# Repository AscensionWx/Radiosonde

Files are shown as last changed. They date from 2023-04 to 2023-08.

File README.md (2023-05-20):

# Radiosonde
Collection of tools for DIY Weather Balloons and Forecasting

For Kanda Weather (Africa) and AscensionWx (U.S.), and open under MIT license.

|  TTGO LoRa32 v2.1     |     Cybaart Kanda Aeolus   |     KandaWeather Launch 
:-------------------------:|:-------------------------:|:-------------------------:
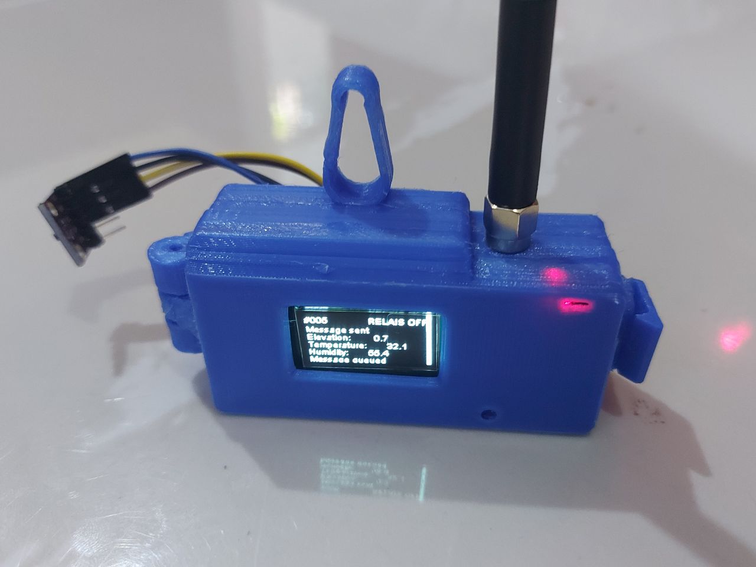
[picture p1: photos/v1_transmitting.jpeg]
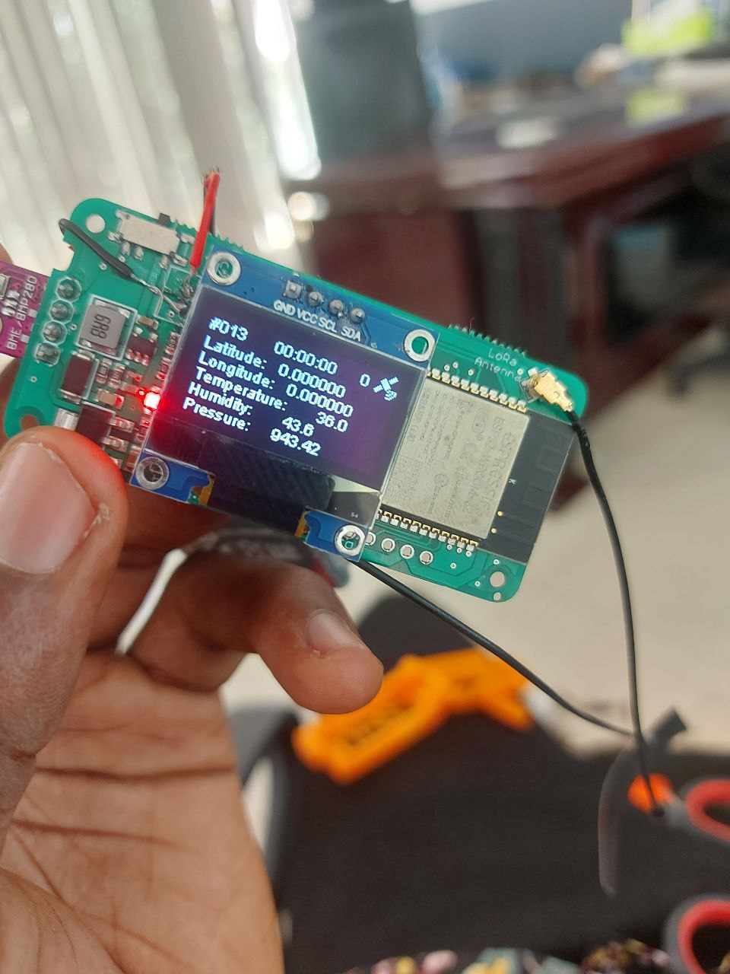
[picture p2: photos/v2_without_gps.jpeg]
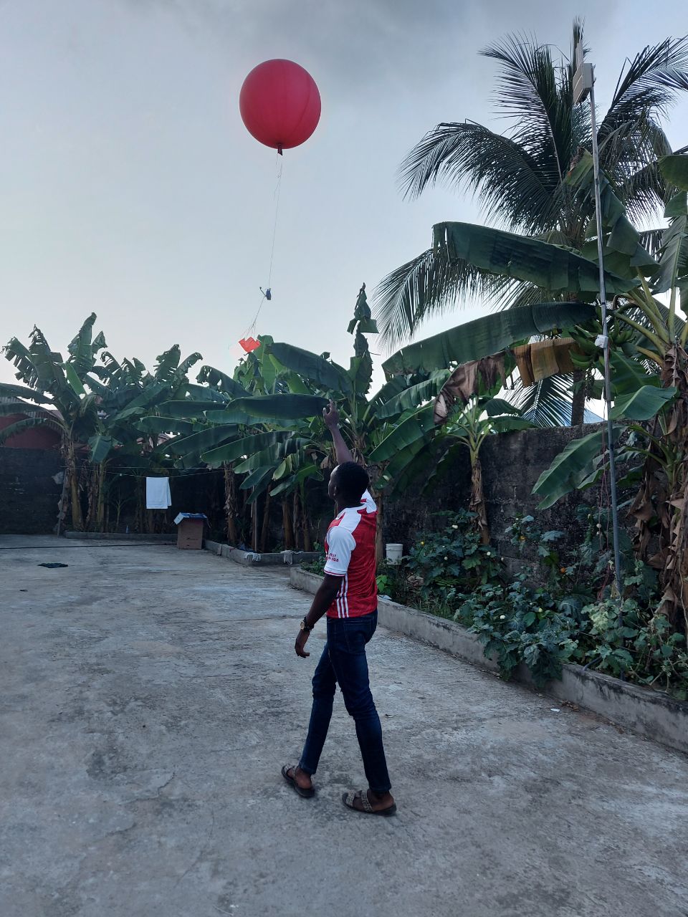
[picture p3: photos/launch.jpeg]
|   |   |   |

Components:
- Hardware
- 3d print files
- Firmware
- LoRaWAN decoders
- Node-red flow files
- Blockchain Smart contract

- Forecasting Dashboard
- Machine Learning Datasets

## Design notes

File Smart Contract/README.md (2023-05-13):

# Smart Contract

The native Antelope C++ smart contract files for AscensionWx Radiosonde Miners.

Features:
- Storage of data from weather balloon launches
- Sends mining rewards in real-time over the course of 90 minutes

Dependencies:
- 1.8.0 eosio CDT

Utilizes other on-chain contracts
- delphioracle
- eosio.evm 

Future additions:
- Device-specific digital signatures

Currently deployed on several contracts such as asensiondal contrct on Telos Mainnet
https://explorer.telos.net/account/ascensiondal

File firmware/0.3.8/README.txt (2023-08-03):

Updates:
Send every 3 seconds for first 150 meters, 5 seconds to 850, 10 seconds to 700, 20 seconds afterwards
checkIfLaunch() function checks if pressure has fallen significantly in 2 consecutive readings
Call checkIfLaunch every 3 seconds while on the ground
Set weather variables as globals
Include -1.0 temperature offset
Apply additional offset based on lux (divide by 9000)
Store 2 minutes of lux
Improve sensor reading handling ... make all global and separate read() functions
Change GPS tx/rx pins to 1 and 3
Submit lat/lon elevation if data ONLY if it's not stale
Light sleep between messages
Set timezone on esp32 and use it when sending observations
We are firmware version 0.3.8, so use ports 81, 82, and 83
Include pressure with status messages that send every 30 seconds
Add unixtime in obs message (since we have GPS and need it for wind)
Add lux avg variable in obs message
Turn wifi off after 2 minutes if no smartphone connected
OLED displays "Turning off screen" for 10 seconds and then turns off
After wifi turn off, sleep between 3-second BME readings and 30-second status msgs
Add time limit check "Time limit reached. Please restart" and sleep

To Do:
Increase power and use SF7 with each transmit e.g. LMIC_setDrTxpow(EU868_DR_SF7, 21)

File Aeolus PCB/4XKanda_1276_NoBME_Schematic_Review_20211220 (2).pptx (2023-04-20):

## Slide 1

4XKanda_1276_NoBME Schematic Review Report

Schematic file: 4XKanda_1276_NoBME.sch
Date: 12/20/2021

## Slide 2

Summary

No. | Description | Status
1 | Incorrect the value of input capacitor (C5, C7, C15, C22) at IC1, IC11, IC16, IC6 (P/N:CJT1117-3.3) | OPEN
2 | Incorrect the value of output capacitor (C6, C8, C16, C23) at IC1, IC11, IC16, IC6 (P/N:CJT1117-3.3) | OPEN
3 | Missing capacitor at VCC pin of IC8, IC13, IC18, IC54 (P/N: ATGM336H) | OPEN
4 | Missing capacitors at “3.3V” pin of U1, U2, U3, U4 (P/N: RFM69HCW-315S2) | OPEN
5 | Missing capacitors at “3.3V” pin of IC3, IC5, IC10, IC15 (P/N: ESP-WROOM-03) | OPEN
6 | High power dissipation at LDO CJT1117-3.3 | OPEN

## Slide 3

Issue 1: Incorrect the value of input capacitor (C5, C7, C15, C22) at IC1, IC11, IC16, IC6
(P/N:CJT1117-3.3)

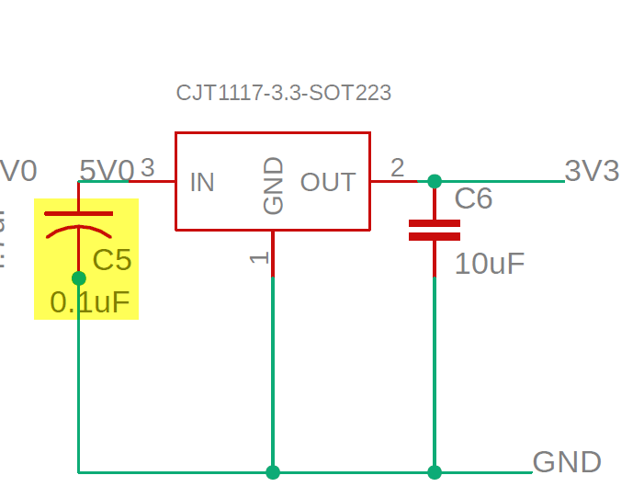
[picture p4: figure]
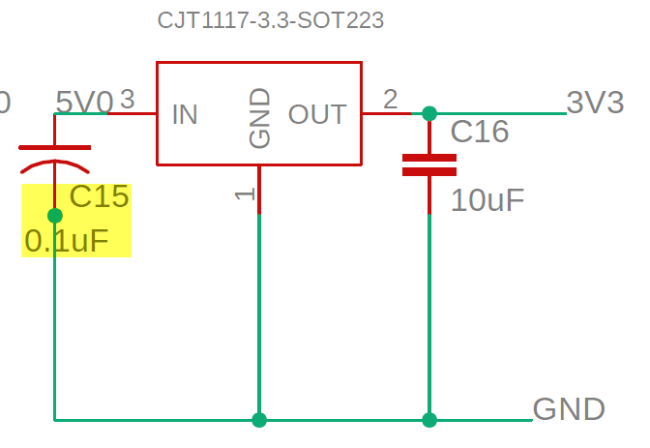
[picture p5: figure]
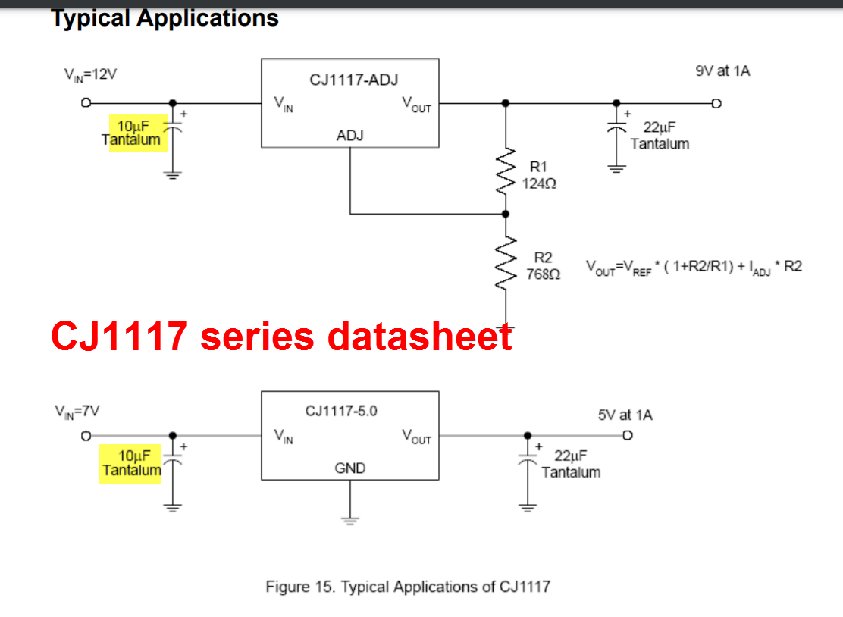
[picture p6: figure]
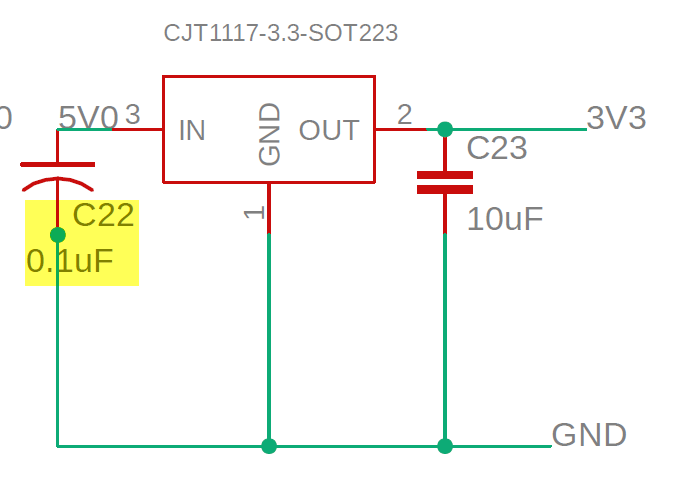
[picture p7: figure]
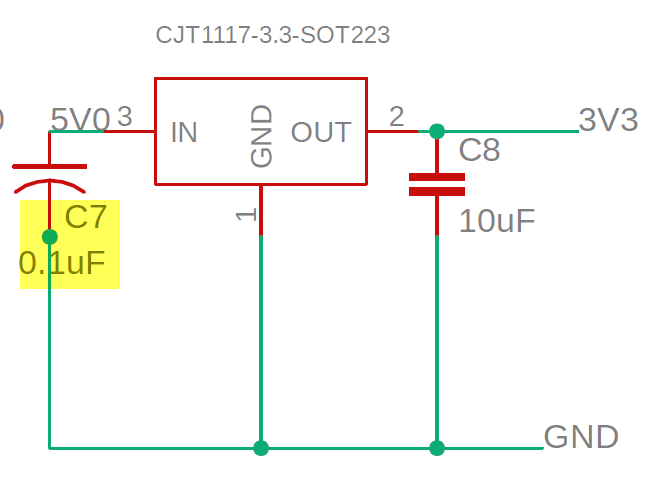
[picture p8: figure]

Per CJ1117 series datasheet, the value of input capacitor (C5, C7, C15, C22) should be 10uF, instead of 0.1uF

Solutions/Recommendation:
Please double check and change the value of C5, C7, C15, C22 to 10uF

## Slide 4

Issue 2: Incorrect the value of output capacitor (C6, C8, C16, C23) at IC1, IC11, IC16, IC6
(P/N:CJT1117-3.3)

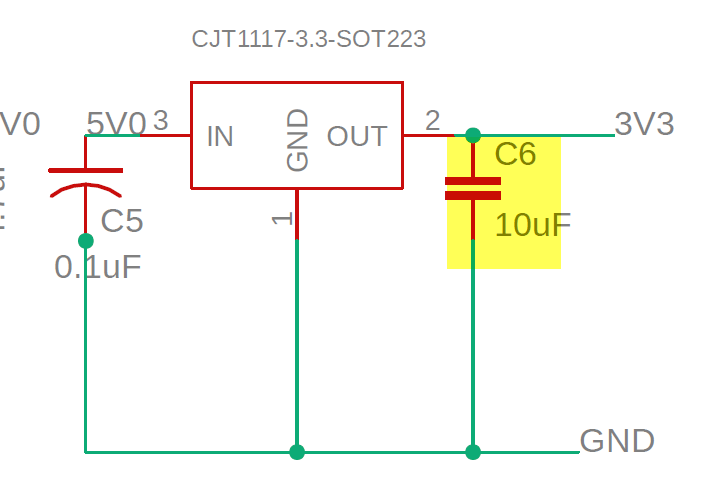
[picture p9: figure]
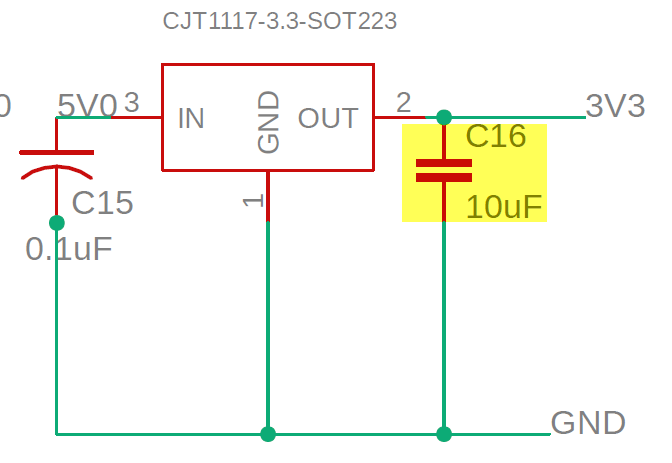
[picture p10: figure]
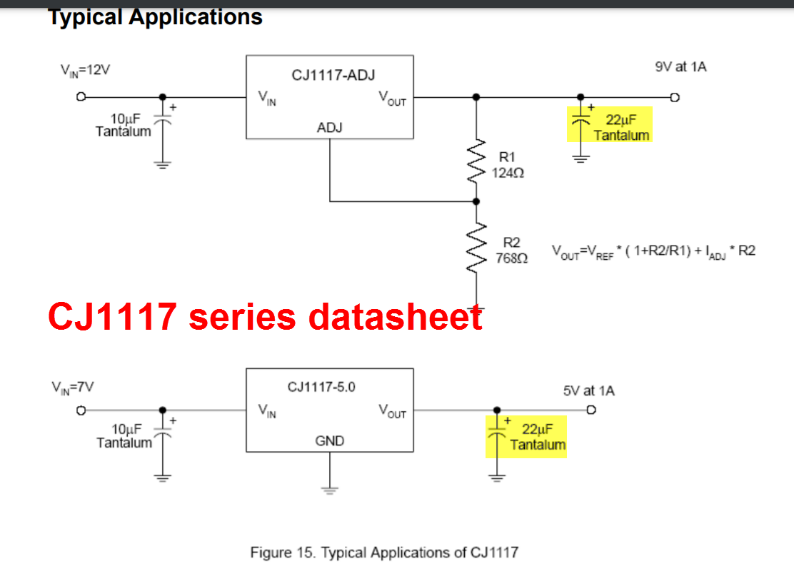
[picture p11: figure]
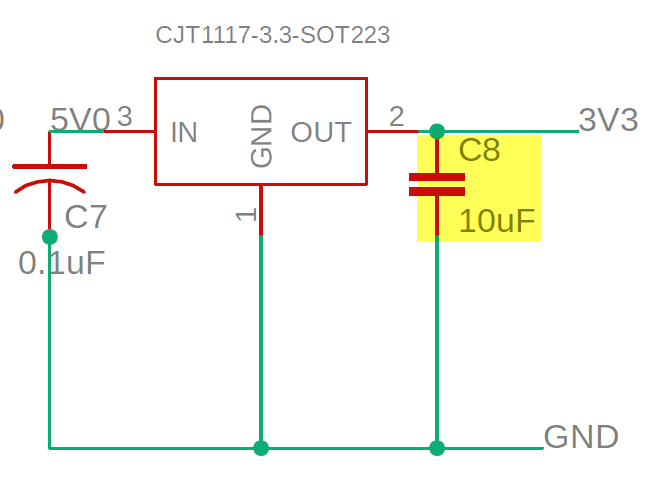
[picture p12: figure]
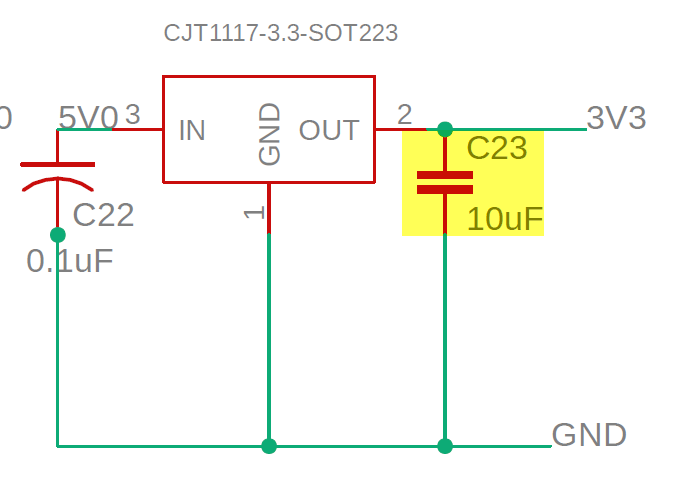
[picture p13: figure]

Per CJ1117 series datasheet, the value of output capacitor (C6, C8, C16, C23) should be 22uF, instead of 10uF

Solutions/Recommendation:
Please double check and change the value of C6, C8, C16, C23 to 22uF

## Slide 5

Issue 3: Missing capacitor at VCC pin of IC8, IC13, IC18, IC54 (P/N: ATGM336H)

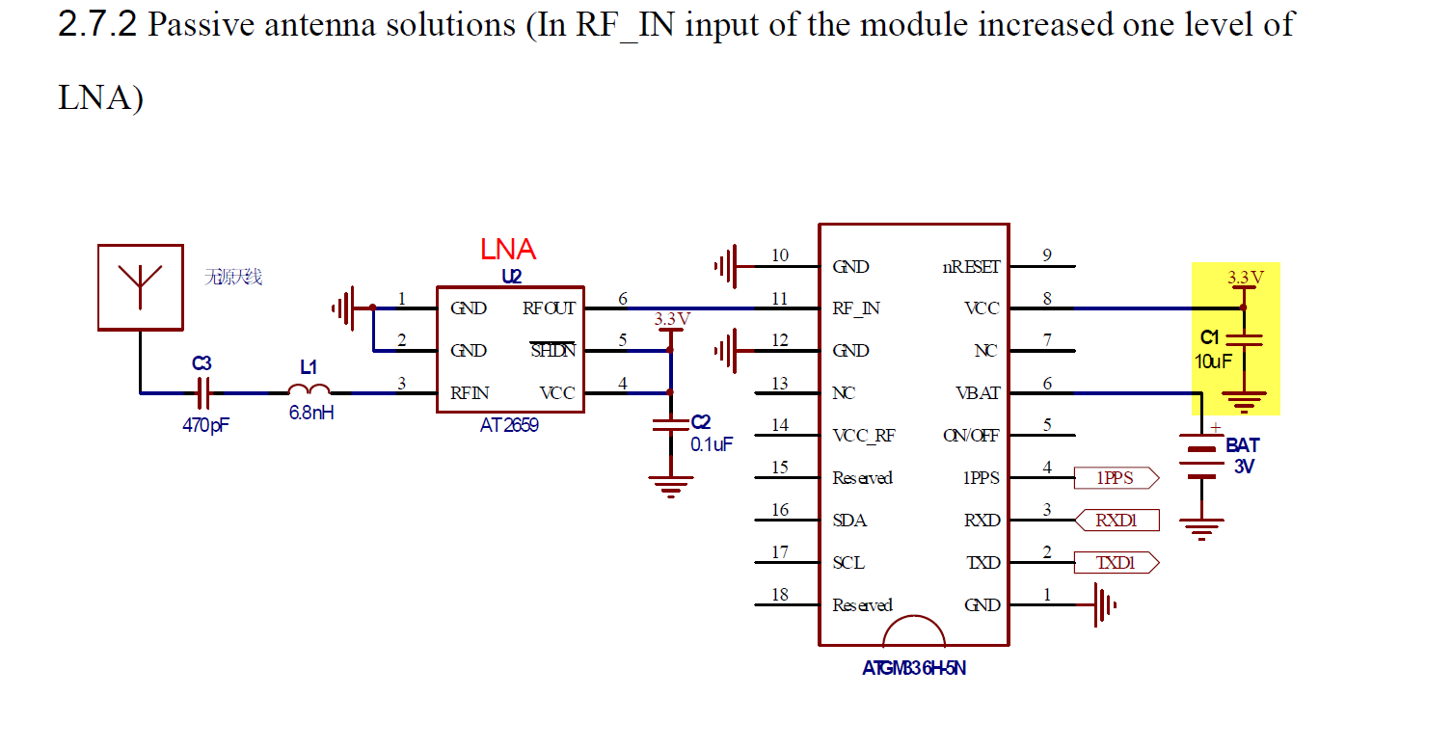
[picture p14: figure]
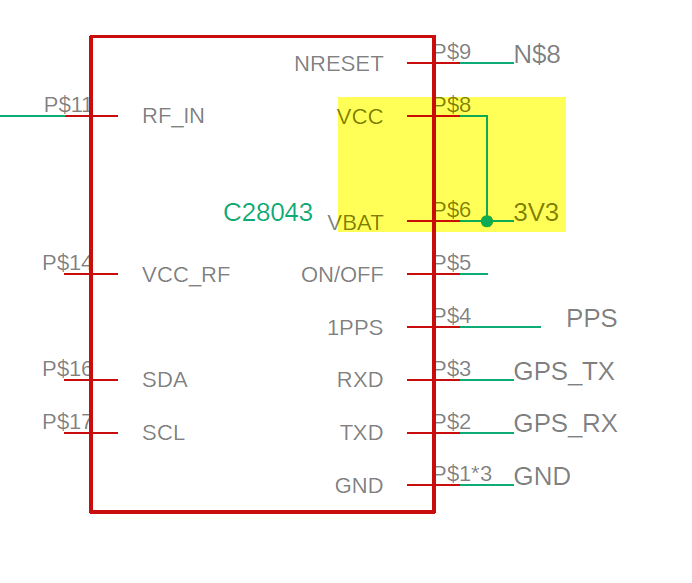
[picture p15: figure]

Solutions/Recommendation:
Please double check and add 10uF at VCC pin of IC8, IC13, IC18, IC54 (P/N: ATGM336H)

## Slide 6

Issue 4: Missing capacitor at “3.3V” pin of U1, U2, U3, U4 (P/N: RFM69HCW-315S2)

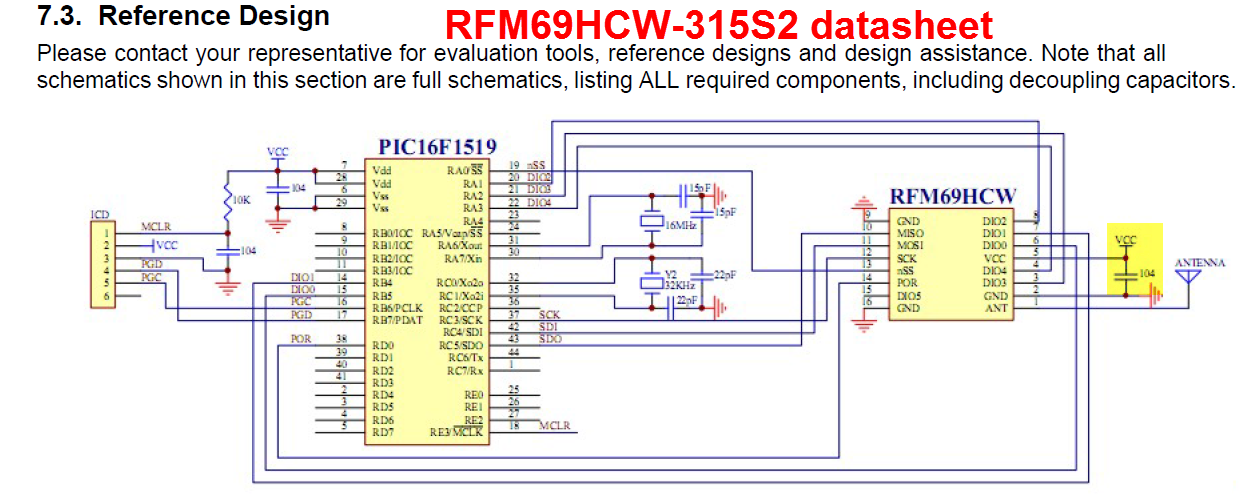
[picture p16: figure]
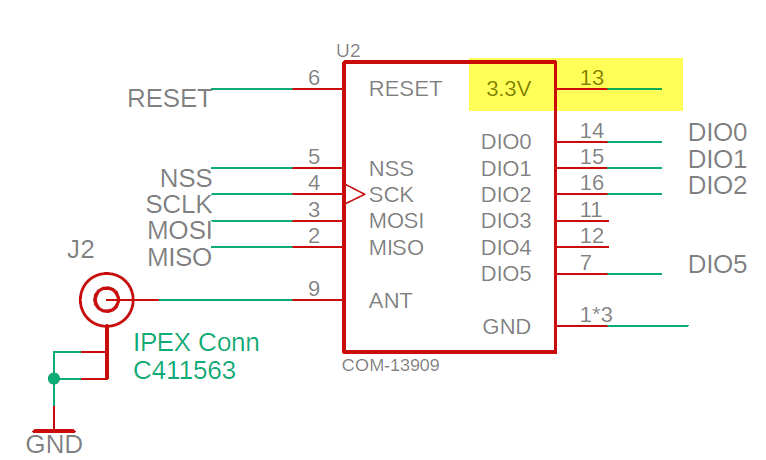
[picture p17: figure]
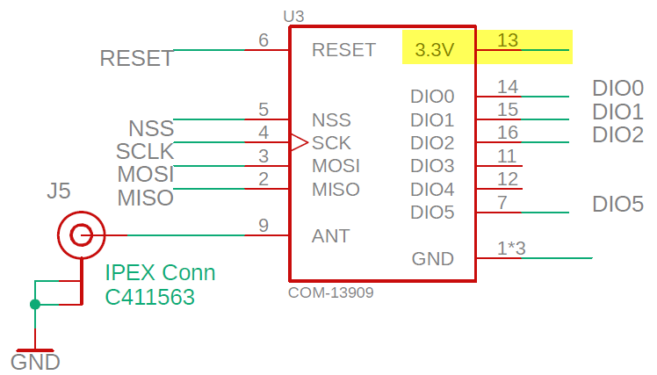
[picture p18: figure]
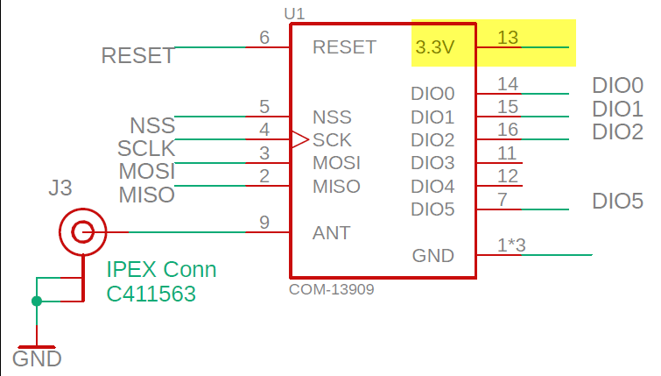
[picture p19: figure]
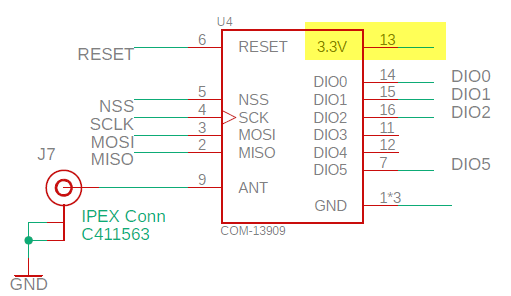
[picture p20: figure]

Solutions/Recommendation:
Please double check and add 0.1uF at “3.3V” pin of U1, U2, U3, U4 (P/N: RFM69HCW-315S2)

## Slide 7

Issue 5: Missing capacitor at “3.3V” pin of IC3, IC5, IC10, IC15 (P/N: ESP-WROOM-03)

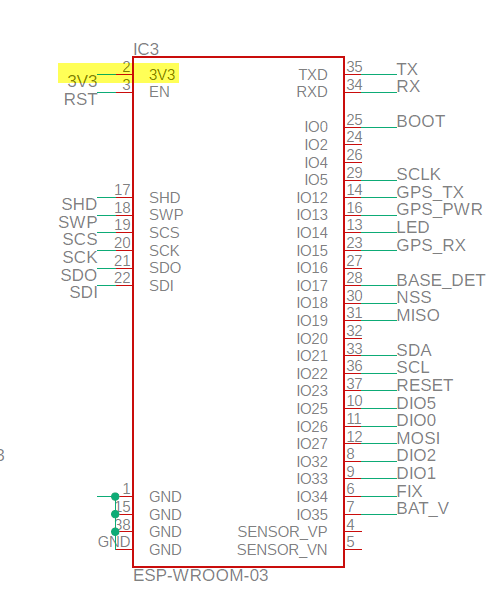
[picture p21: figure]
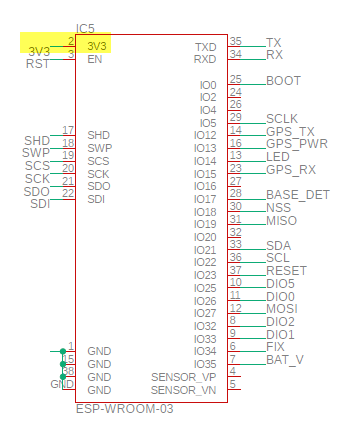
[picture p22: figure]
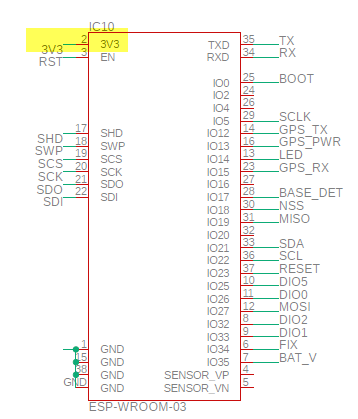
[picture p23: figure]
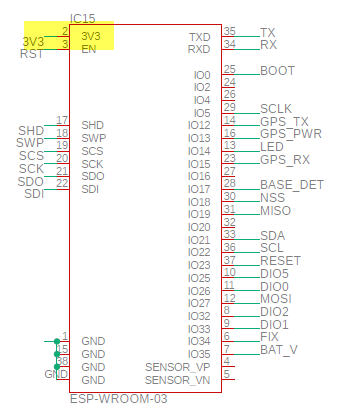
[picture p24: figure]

Solutions/Recommendation:
Please double check and add 0.1uF at “3.3V” pin of IC3, IC5, IC10, IC15 (P/N: ESP-WROOM-03)

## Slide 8

Issue 6: High power dissipation at LDO CJT1117-3.3

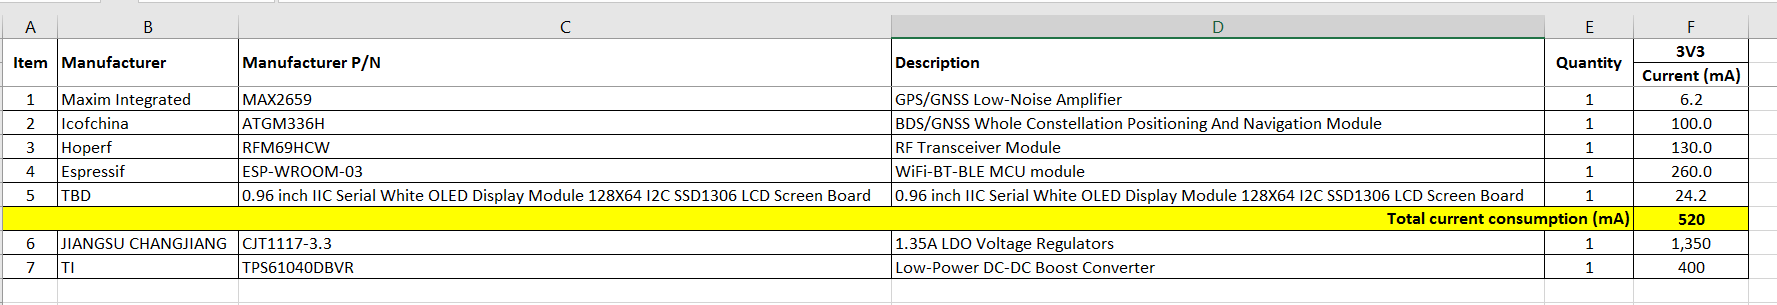
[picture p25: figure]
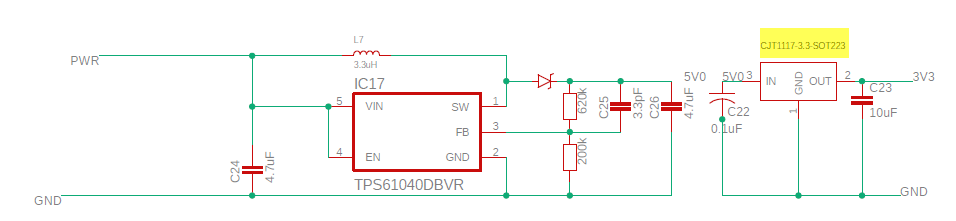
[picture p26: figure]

The maximum power consumption on each module is calculated about 520mA. The power dissipation at LDO
CJT1117-3.3 is about (5-3.3)*0.52 = 0.88W. This may cause hot issue.
One more thing, the maximum current consumption of 5V0 rail is 520mA. But the maximum output current of Boost converter (TPS61040DBVR) is 400mA. Please double check

Solutions/Recommendation:
We need to re-design the board with a new buck regulator (example ADP2107ACPZ-3-3-R7 (https://www.digikey.com/en/products/detail/analog-devices-inc/ADP2107ACPZ-3-3-R7/1166727) if VIN > 3.6V) or a new boost/buck regulator (example LTC3538EDCB-TRPBF (https://www.digikey.com/en/products/detail/analog-devices-inc/LTC3538EDCB-TRPBF/1746127)).
Please provide characteristics of power input (voltage range, ripple noise), then we will study and provide the best solution.

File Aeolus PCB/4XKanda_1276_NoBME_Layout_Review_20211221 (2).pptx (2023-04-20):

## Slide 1

4XKanda_1276_NoBME Layout Review Report

Layout file : 4XKanda_1276_NoBME.brd
Date: 12/21/2021

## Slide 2

Summary

No. | Description | Status
1 | Copper to copper spacing is too small (~ 2 mils minimum). | OPEN
2 | Copper touched to the solder mask opening. | OPEN
3 | The antenna RF trace and 3V3 trace routed in the keep-out area of ESP32-WROOM-32 module | OPEN
4 | Missing GND via for the thermal pad of ESP32-WROOM-32 module. | OPEN
5 | The antenna RF trace of module RFM69HCW ISM Transceiver (PN: COM-13909) routed in the antenna area of ESP32-WROOM-32 module. | OPEN
6 | The trace routed too close to non-plated through hole (~3.6 mils) . | OPEN
7 | The placement and routing for GPS’ antenna is not good. | OPEN
8 | The solder mask web is too small ( ~ 1.8 mils minimum). | OPEN

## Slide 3

Issue 1: Copper to copper spacing is too small

The copper to copper spacing is less than 4 mils in some areas below. Especially, it’s only 2mil spacing found. It’s a very risk that causes the potential shorted net in the manufacturing process. The shorted net is one of the reasons for PCB hot and failure.

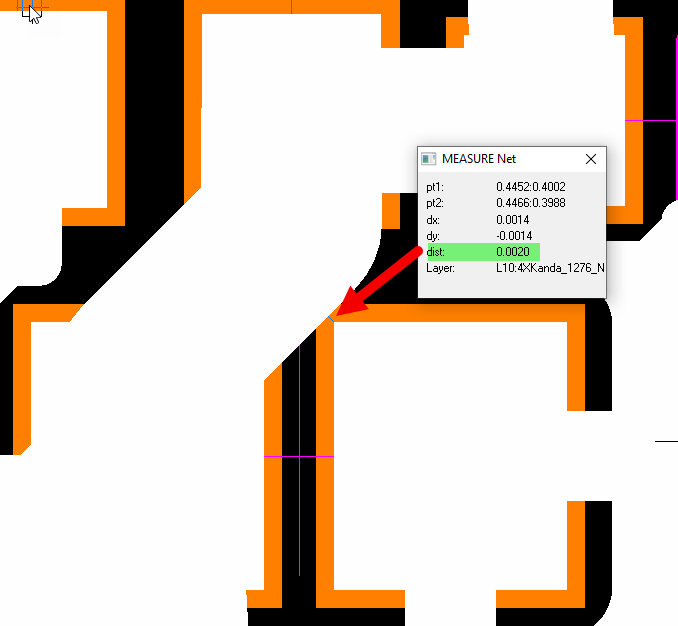
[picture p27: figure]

Solutions/Recommendation:
Keep copper to copper spacing to 5 mils minimum.

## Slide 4

Issue 2: Copper touched the solder mask opening.
This cause the potential solder bridging during assembly.


Solutions/Recommendation:
Move the copper out of the pad solder mask.
Do not route trace/copper running underneath the discrete components

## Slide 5

Issue 3: The antenna RF trace and 3V3 trace routed in the keepout area (Antenna area) of ESP32-WROOM-32 module.
This is the potential RF noise issue and RF antenna sensitivity reduction.


Solutions/Recommendation:
Move all signal trace/power trace out of the antenna keepout area per datasheet recommended.

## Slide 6

Issue 4: Missing GND vias for thermal pad of ESP32-WROOM-32 module.


Solutions/Recommendation:
To improve thermal dissipation performance:
Add more vias for thermal pad per datasheet recommended
Suggest to connect thermal pad to full copper planes, no thermal spoke as the current layout


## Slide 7

Issue 5: The antenna RF trace of module RFM69HCW ISM Transceiver (PN: COM-13909) routed in the antenna area of ESP32-WROOM-32 module.
This is the potential RF noise issue and RF antenna sensitivity reduction.


Solutions/Recommendation:
Move the antenna connector (IPEX Conn C411563) to close to the antenna pin of the module RFM69HCW on the bottom side.
Route the antenna trace length as short as possible without transition via as example below.


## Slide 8

Issue 6: The trace routed too close to non-plated through hole (~3.6 mils).


Solutions/Recommendation:
We recommend to keep 8-10 mils copper spacing to non-plated through hole to void the fab/assembly DFM issues.

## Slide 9

Issue 7: The placement and routing for GPS antenna is not good


Solutions/Recommendation:
We recommend to re-do layout for GPS antenna as below to improve the RF antenna sensitivity.


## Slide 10

Issue 8: The solder mask web is too small ( ~ 1.8 mils minimum).
This cause the potential solder bridging during assembly.


Solutions/Recommendation:
Keep the solder mask web to 3 mils minimum per DFM rule so that we have the solder mask dam between two pads to avoid the potential solder bridging during assembly.

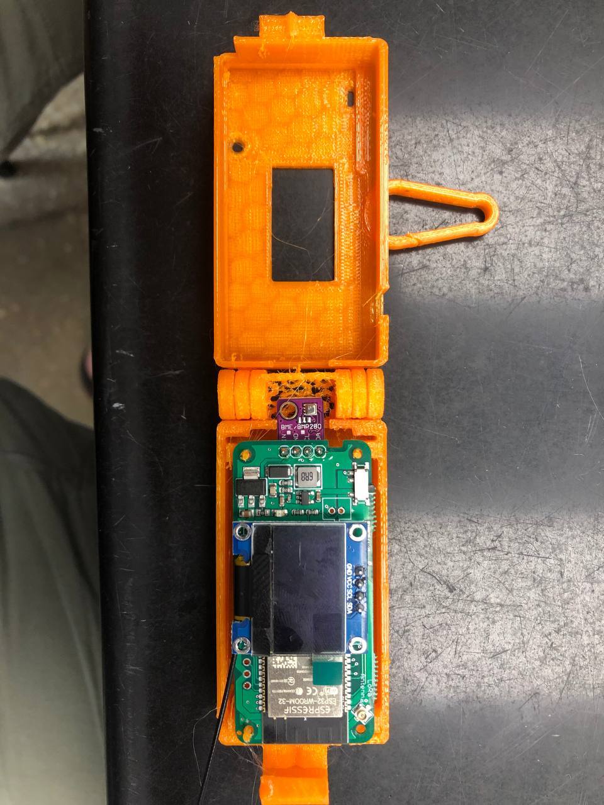
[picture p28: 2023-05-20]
photos/v2_board_with_enclosure.jpg

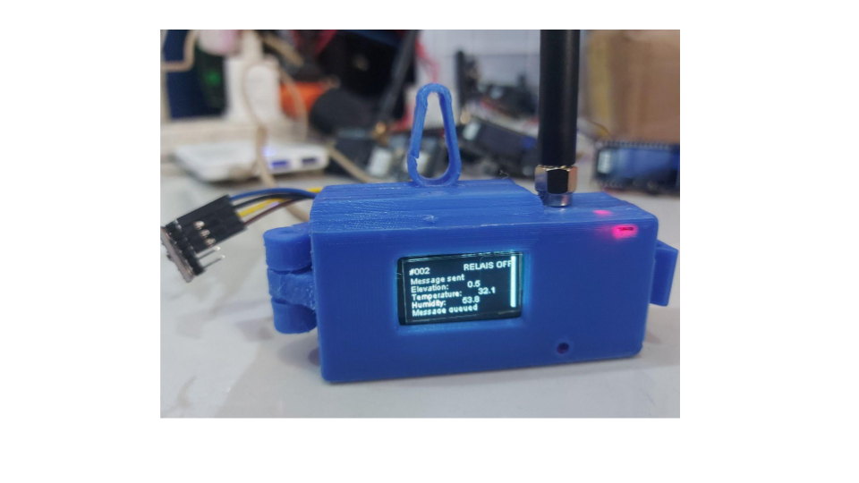
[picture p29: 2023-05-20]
photos/lora32_transmitting.png

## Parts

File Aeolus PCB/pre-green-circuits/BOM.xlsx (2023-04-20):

Comment | Designator | Footprint | LCSC Part #（optional）
4.7uF | C1, C3, C10, C12, C17, C19, C24, C26 | C0603 | C19666
3.3pF | C2, C11, C18, C25 | C0402 | C1565
0.1uF | C5, C7, C15, C22 | C0805 | C49678
10uF | C6, C8, C16, C23 | C0805 | C15850
0.1uF | C4, C13, C20, C27 | C0603 | C14663
470pF | C9, C14, C21, C28 | C0603 | C1620
BA340A | D1, D2, D3, D4 | SMA-DIODE | C22452
CJT1117-3.3-SOT223 | IC1, IC6, IC11, IC16 | SOT-223 | C6186
TPS61040DBVR | IC2, IC7, IC12, IC17 | SOT23-5 | C7722
ESP32 | IC3, IC5, IC10, IC15 | QFN-38 | C82899
MAX2659 | IC4, IC9, IC14, IC19 | UDFN-6 | C28043
ATMG336H | IC8, IC13, IC18, IC54 | QFN-18 | C90770
U.FL | J1, J2, J3, J4, J5, J6, J7, J8 | SMD-3 | C496552
3.3uH | L1, L3, L5, L7 | 4.2X4.2 | C408338
6.8uH | L2, L4, L6, L8 | I0402 | C32041
BLUE | LED1,LED5,LED9,LED13 | LED0805 | C2293
RED | LED2,LED6,LED10,LED14 | LED0805 | C84256
YELLOW | LED3,LED7,LED11,LED15 | LED0805 | C2296
GREEN | LED4,LED8,LED12,LED16 | LED0805 | C2297
620k | R1, R8, R23, R34 | R0603 | C23219
2K | R11, R20, R31, R42 | R0603 | C22975
200k | R2, R13, R24, R35 | R0603 | C25811
1K | R4, R5, R9, R12, R15, R16, R19, R21, R26, R27, R30, R32, R37, R38, R41, R43 | R0603 | C21190
1K | R3, R7, R10, R14, R18, R22, R25, R29, R33, R36, R40, R44 | R0603 | C21190
2K | R6, R17, R28, R39 | R0603 | C22975
SMD-SWITCH | S1,S2,S3,S4 | SMD-3 | C431541

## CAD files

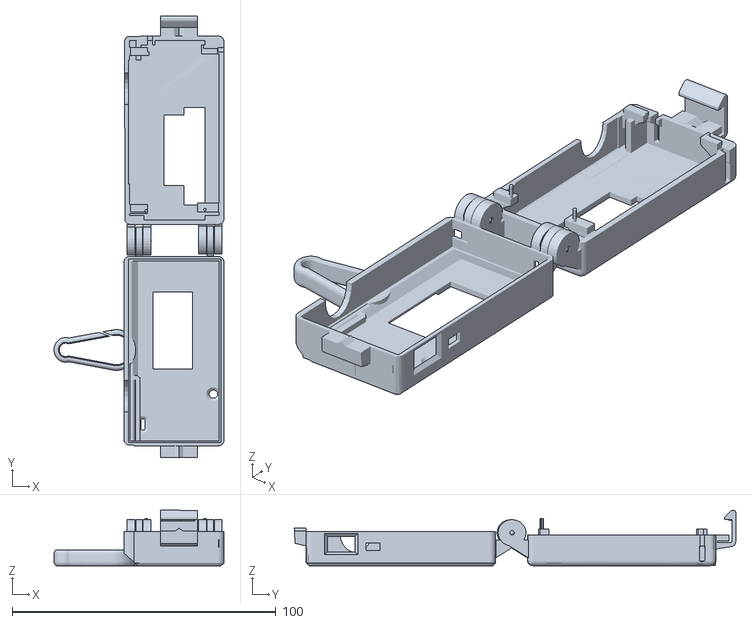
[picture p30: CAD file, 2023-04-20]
Enclosure 3D-print files/Balloon Payload TTGO LoRa32.stl
64.5 x 167.4 x 21.0

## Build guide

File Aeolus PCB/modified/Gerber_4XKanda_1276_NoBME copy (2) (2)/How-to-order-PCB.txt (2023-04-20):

How to Order PCB

Please refer to:
https://docs.easyeda.com/en/PCB/Order-PCB

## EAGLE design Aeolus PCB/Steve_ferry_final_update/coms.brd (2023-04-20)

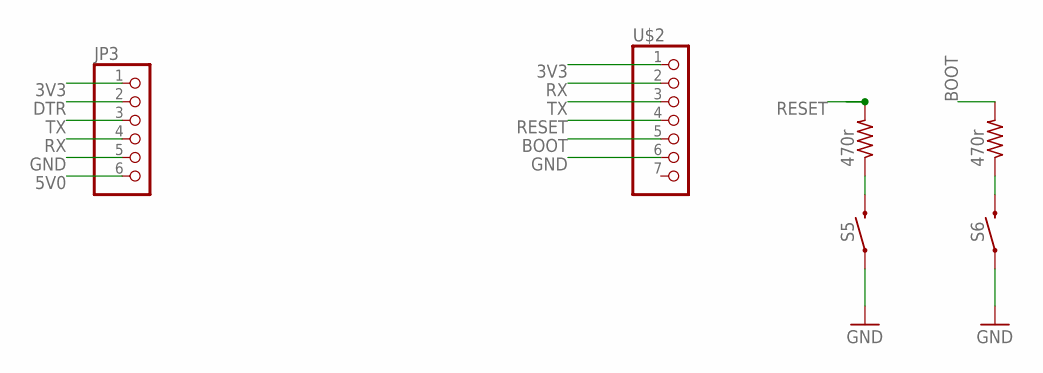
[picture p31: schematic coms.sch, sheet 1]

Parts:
JP3: HEADER-1X6ROUND; 1X06_ROUND
R5, R6: 470r; M1206
S5, S6: MOMENTARY-SWITCH-SPST; TACTILE_SWITCH_C480275
U$2: HEADER-1X7ROUND; 1X07_ROUND

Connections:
3V3: JP3.1, U$2.1; also elsewhere on the board
5V0: JP3.6; also elsewhere on the board
BOOT: R6.2, U$2.5; also elsewhere on the board
DTR: JP3.2; also elsewhere on the board
GND: JP3.5, S5.1, S5.2 (1), S6.1, S6.2 (1), U$2.6; also elsewhere on the board
unnamed: R5.1, S5.3 (2), S5.4 (2)
unnamed: R6.1, S6.3 (2), S6.4 (2)
RESET: R5.2, U$2.4; also elsewhere on the board
RX: JP3.4, U$2.2; also elsewhere on the board
TX: JP3.3, U$2.3; also elsewhere on the board

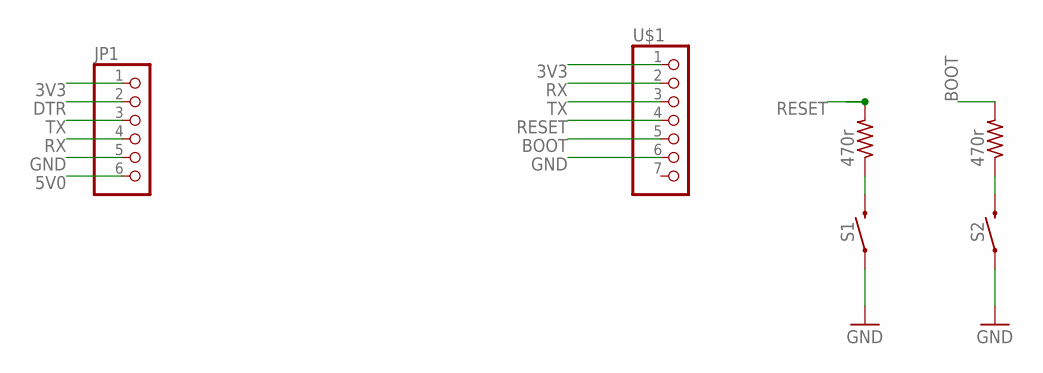
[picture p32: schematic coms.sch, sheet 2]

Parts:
JP1: HEADER-1X6ROUND; 1X06_ROUND
R1, R2: 470r; M1206
S1, S2: MOMENTARY-SWITCH-SPST; TACTILE_SWITCH_C480275
U$1: HEADER-1X7ROUND; 1X07_ROUND

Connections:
3V3: JP1.1, U$1.1; also elsewhere on the board
5V0: JP1.6; also elsewhere on the board
BOOT: R2.2, U$1.5; also elsewhere on the board
DTR: JP1.2; also elsewhere on the board
GND: JP1.5, S1.1, S1.2 (1), S2.1, S2.2 (1), U$1.6; also elsewhere on the board
unnamed: R1.1, S1.3 (2), S1.4 (2)
unnamed: R2.1, S2.3 (2), S2.4 (2)
RESET: R1.2, U$1.4; also elsewhere on the board
RX: JP1.4, U$1.2; also elsewhere on the board
TX: JP1.3, U$1.3; also elsewhere on the board

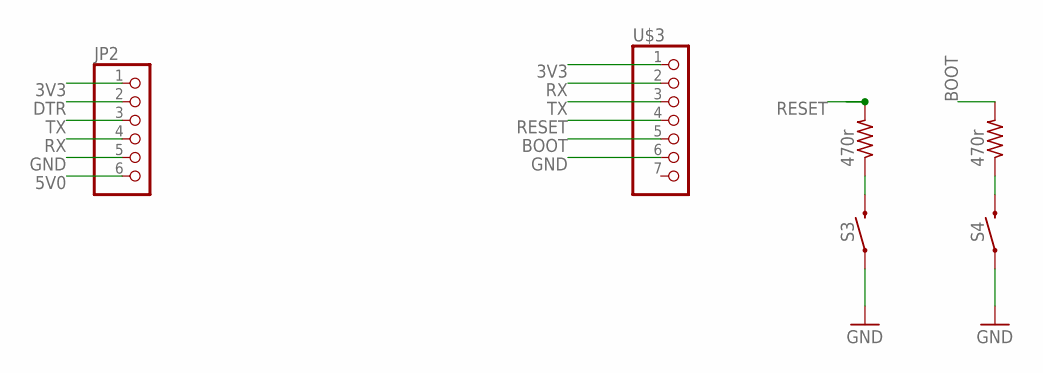
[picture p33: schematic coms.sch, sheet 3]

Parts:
JP2: HEADER-1X6ROUND; 1X06_ROUND
R3, R4: 470r; M1206
S3, S4: MOMENTARY-SWITCH-SPST; TACTILE_SWITCH_C480275
U$3: HEADER-1X7ROUND; 1X07_ROUND

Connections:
3V3: JP2.1, U$3.1; also elsewhere on the board
5V0: JP2.6; also elsewhere on the board
BOOT: R4.2, U$3.5; also elsewhere on the board
DTR: JP2.2; also elsewhere on the board
GND: JP2.5, S3.1, S3.2 (1), S4.1, S4.2 (1), U$3.6; also elsewhere on the board
unnamed: R3.1, S3.3 (2), S3.4 (2)
unnamed: R4.1, S4.3 (2), S4.4 (2)
RESET: R3.2, U$3.4; also elsewhere on the board
RX: JP2.4, U$3.2; also elsewhere on the board
TX: JP2.3, U$3.3; also elsewhere on the board

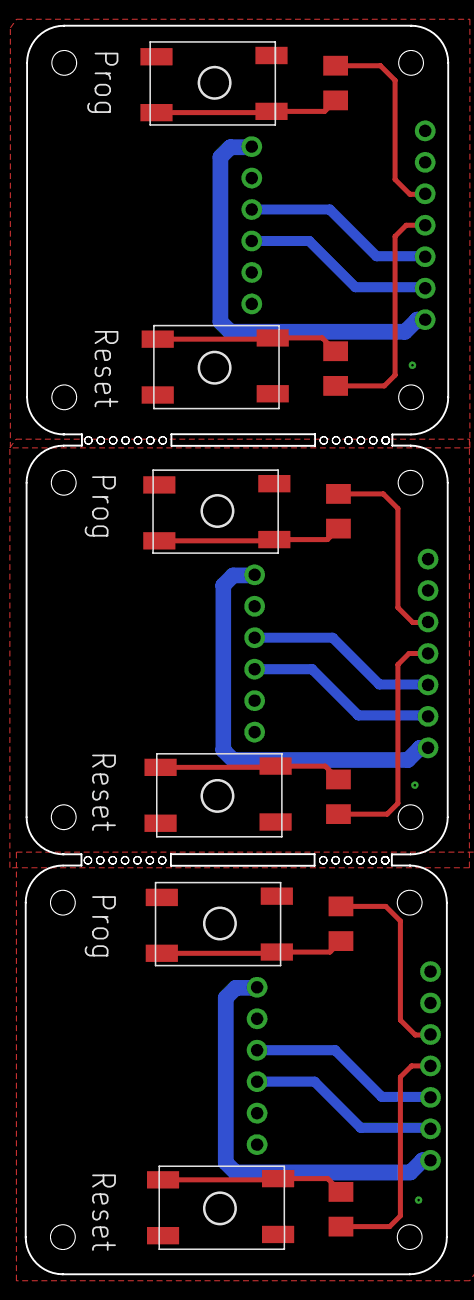
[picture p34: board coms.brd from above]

Board: 2 copper layers, 34.1 x 100.8 mm, 18 parts (0 on the bottom side), 14 nets.

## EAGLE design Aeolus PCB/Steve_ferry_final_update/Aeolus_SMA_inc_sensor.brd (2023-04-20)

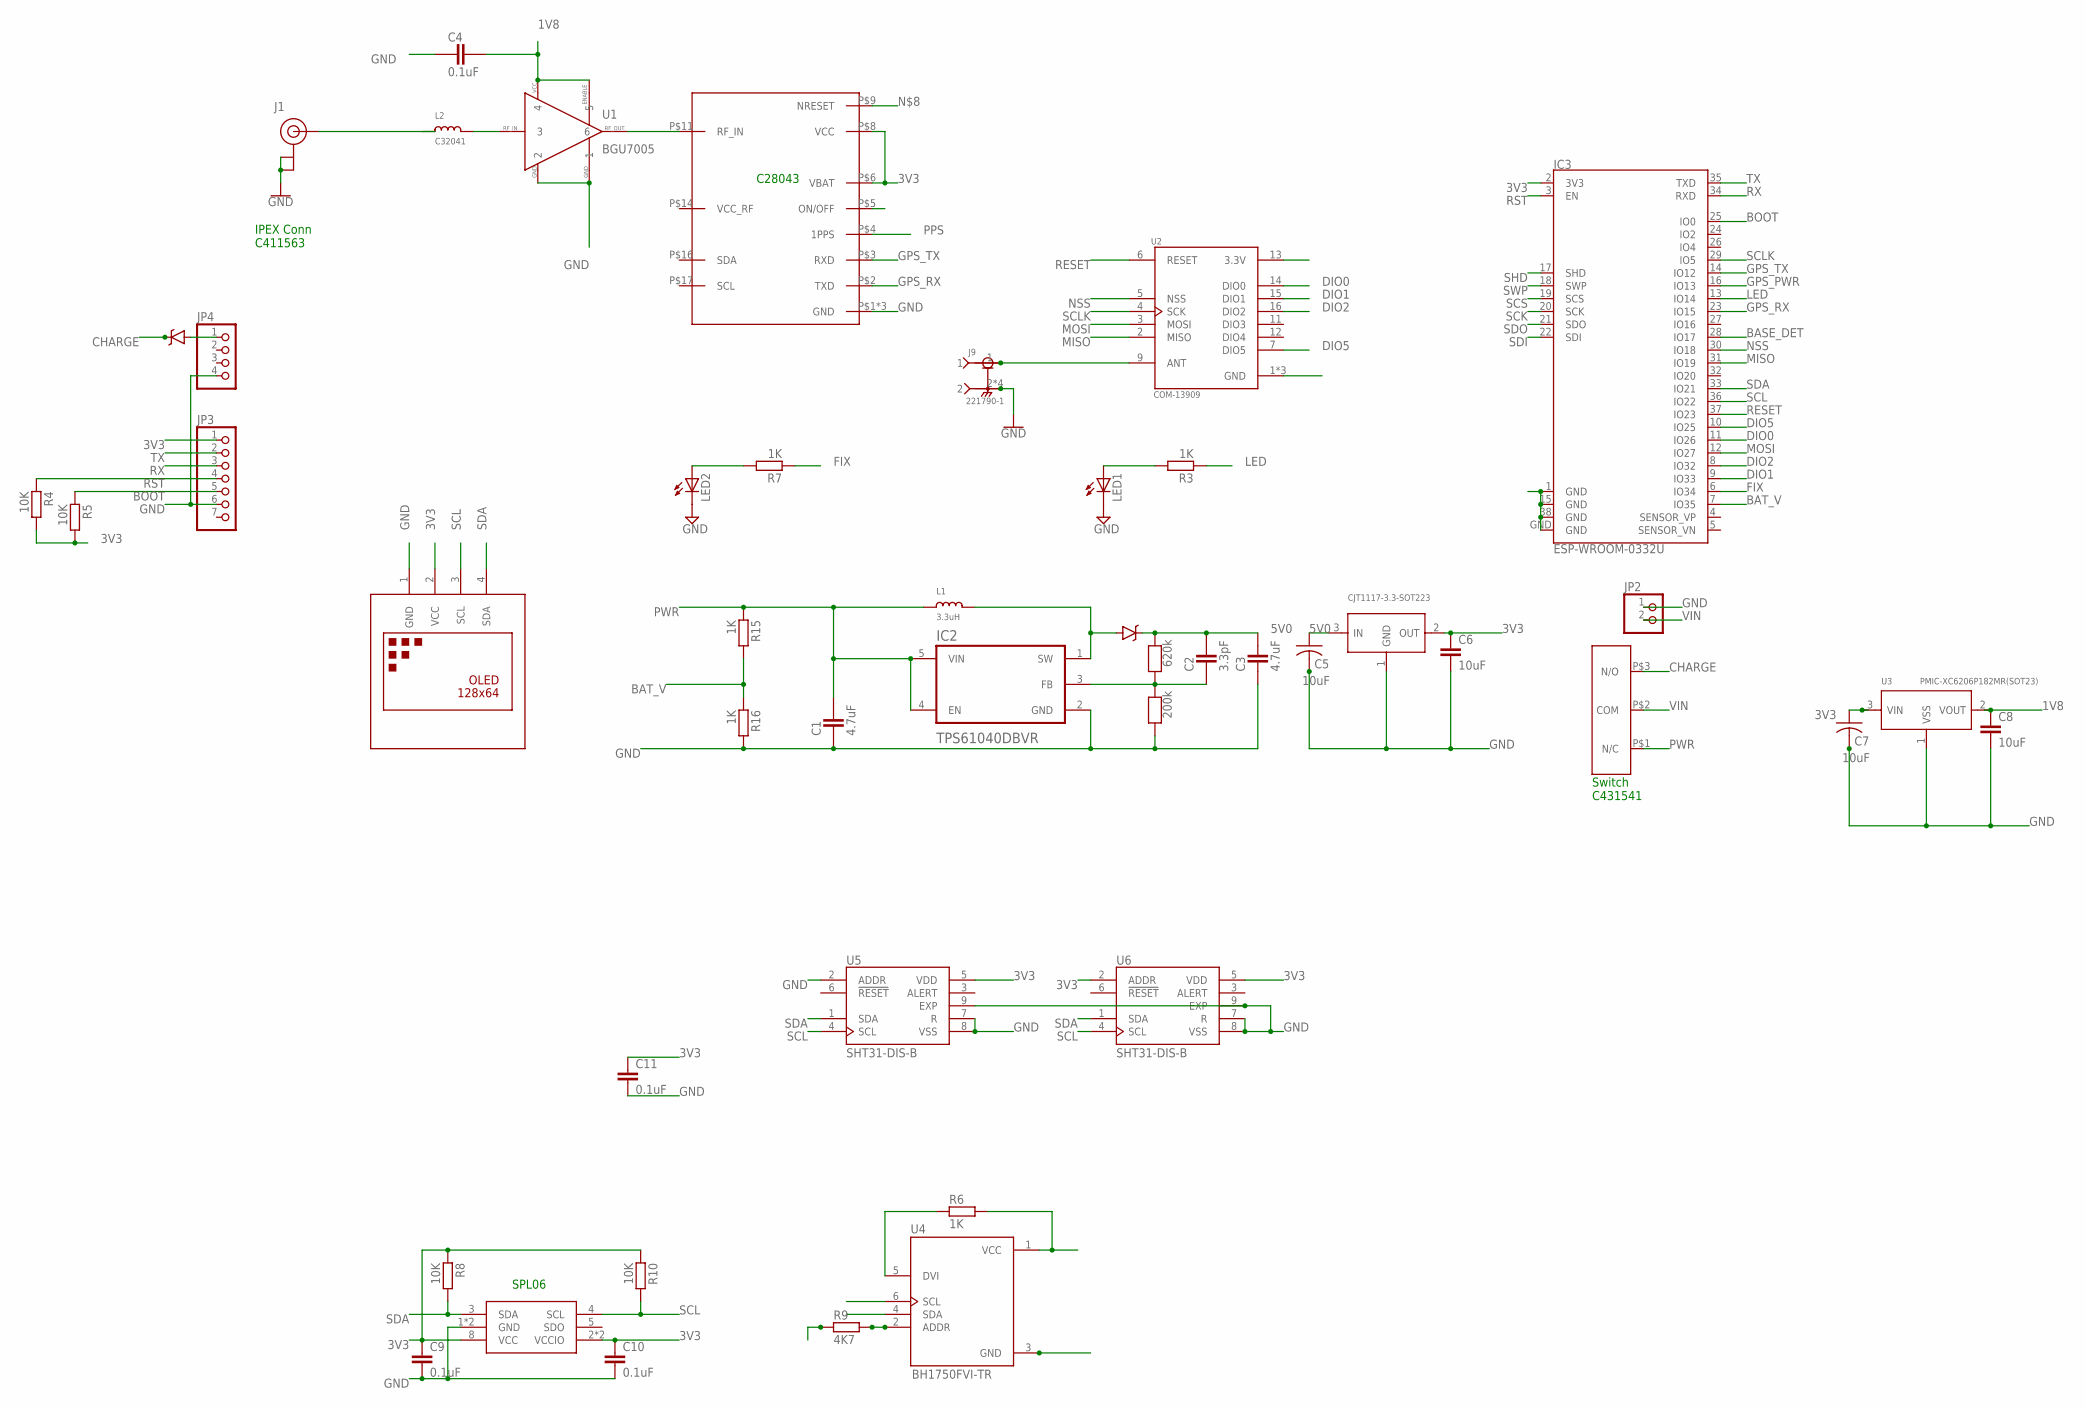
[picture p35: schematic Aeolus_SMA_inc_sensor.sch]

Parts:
C1, C3: 4.7uF; CAPC1608X92N
C2: 3.3pF; CAPC1005X60N
C4: 0.1uF; CAPC1608X92N
C5: 10uF; C0805
C6: 10uF; C0805@1
C7: 10uF; C0402
C8: 10uF; C0402K@1
C9, C10, C11: 0.1uF; C0603@1
D1, D2: BA340A; SMA-DIODE
IC1: CJT1117-3.3-SOT223; SOT-223
IC2: TPS61040DBVR; SOT95P280X145-5N
IC3: ESP-WROOM-0332U; ESP32-WROOM-32U
IC54: ATGM336H
J1: U.FL
J9: 221790-1; TE_221790-1
JP2: HEADER-1X2ROUND; 1X02_ROUND
JP3: HEADER-1X7ROUND; 1X07_ROUND
JP4: HEADER-1X4ROUND; 1X04_ROUND
L1: 3.3uH; INDUCTOR_5X5MM_NR5040_NOTHERMALS
L2: C32041; _0402
LED1, LED2: LEDSML0805; SML0805
R1: 620k; 0603
R2: 200k; 0603
R3, R6, R7, R15, R16: 1K; RESC1608X55N
R4, R5, R8, R10: 10K; RESC1608X55N
R9: 4K7; RESC1608X55N
S1: SMD-SWITCH
U1: BGU7005; SOT886
U2: COM-13909; MOD_COM-13909
U3: PMIC-XC6206P182MR(SOT23); SOT-23
U4: BH1750FVI-TR; XDCR_BH1750FVI-TR
U5, U6: SHT31-DIS-B; SON50P250X250X100-9N
U$1: DISPLAY-OLED-128X64-I2C
U$4: SPL06

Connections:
1V8: C4.2, C8.1, U1.4, U1.5, U3.2 (VOUT)
3V3: C6.1, C7.1, C9.1, C10.1, C11.1, IC1.2 (OUT), IC3.2 (3V3), IC54.P$6 (VBAT), IC54.P$8 (VCC), JP3.1, R4.2, R5.2, R6.2, R8.1, R10.1, U2.13 (3.3V), U3.3 (VIN), U4.1 (VCC), U5.5 (VDD), U6.2 (ADDR), U6.5 (VDD), U$1.2 (VCC), U$4.2 (VCCIO), U$4.6 (VCCIO), U$4.8 (VCC)
5V0: C2.2, C3.2, C5.1, D1.C, IC1.3 (IN), R1.1
ANT: J9.1, U2.9 (ANT)
BASE_DET: IC3.28 (IO17)
BAT_V: IC3.7 (IO35), R15.2, R16.1
BOOT: IC3.25 (IO0), JP3.5, R5.1
CHARGE: D2.C, S1.P$3 (N/O)
DIO0: IC3.11 (IO26), U2.14 (DIO0)
DIO1: IC3.9 (IO33), U2.15 (DIO1)
DIO2: IC3.8 (IO32), U2.16 (DIO2)
DIO5: IC3.10 (IO25), U2.7 (DIO5)
FB: C2.1, IC2.3 (FB), R1.2, R2.1
FIX: IC3.6 (IO34), R7.1
GND: C1.1, C3.1, C4.1, C5.2, C6.2, C7.2, C8.2, C9.2, C10.2, C11.2, IC1.1 (GND), IC2.2 (GND), IC3.1 (GND), IC3.15 (GND), IC3.38 (GND), IC3.GND, IC54.P$1 (GND), IC54.P$10 (GND), IC54.P$12 (GND), J1.1 (GND), J1.2 (GND), J9.2, J9.3 (2), J9.4 (2), J9.5 (2), JP2.1, JP3.6, JP4.4, LED1.C, LED2.C, R2.2, R9.1, R16.2, U1.1, U1.2, U2.1 (GND), U2.8 (GND), U2.10 (GND), U3.1 (VSS), U4.3 (GND), U5.2 (ADDR), U5.7 (R), U5.8 (VSS), U5.9 (EXP), U6.7 (R), U6.8 (VSS), U6.9 (EXP), U$1.1 (GND), U$4.1 (GND), U$4.7 (GND)
GPS_PWR: IC3.16 (IO13)
GPS_RX: IC3.23 (IO15), IC54.P$2 (TXD)
GPS_TX: IC3.14 (IO12), IC54.P$3 (RXD)
LED: IC3.13 (IO14), R3.1
MISO: IC3.31 (IO19), U2.2 (MISO)
MOSI: IC3.12 (IO27), U2.3 (MOSI)
unnamed: D1.A, IC2.1 (SW), L1.P$2 (2)
unnamed: D2.A, JP4.1
unnamed: LED1.A, R3.2
unnamed: J1.FEED (SIGNAL), L2.1
unnamed: LED2.A, R7.2
unnamed: IC54.P$11 (RF_IN), U1.6
unnamed: R6.1, U4.5 (DVI)
unnamed: L2.2, U1.3
unnamed: R9.2, U4.2 (ADDR)
NSS: IC3.30 (IO18), U2.5 (NSS)
PPS: IC54.P$4 (1PPS)
PWR: C1.2, IC2.4 (EN), IC2.5 (VIN), L1.P$1 (1), R15.1, S1.P$1 (N/C)
RESET: IC3.37 (IO23), U2.6 (RESET)
RST: IC3.3 (EN), JP3.4, R4.1
RX: IC3.34 (RXD), JP3.3
SCK: IC3.20 (SCK)
SCL: IC3.36 (IO22), R10.2, U4.6 (SCL), U5.4 (SCL), U6.4 (SCL), U$1.3 (SCL), U$4.4 (SCL)
SCLK: IC3.29 (IO5), U2.4 (SCK)
SCS: IC3.19 (SCS)
SDA: IC3.33 (IO21), R8.2, U4.4 (SDA), U5.1 (SDA), U6.1 (SDA), U$1.4 (SDA), U$4.3 (SDA)
SDI: IC3.22 (SDI)
SDO: IC3.21 (SDO)
SHD: IC3.17 (SHD)
SWP: IC3.18 (SWP)
TX: IC3.35 (TXD), JP3.2
VIN: JP2.2, S1.P$2 (COM)

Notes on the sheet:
Switch C431541
IPEX Conn C411563
C28043
SPL06

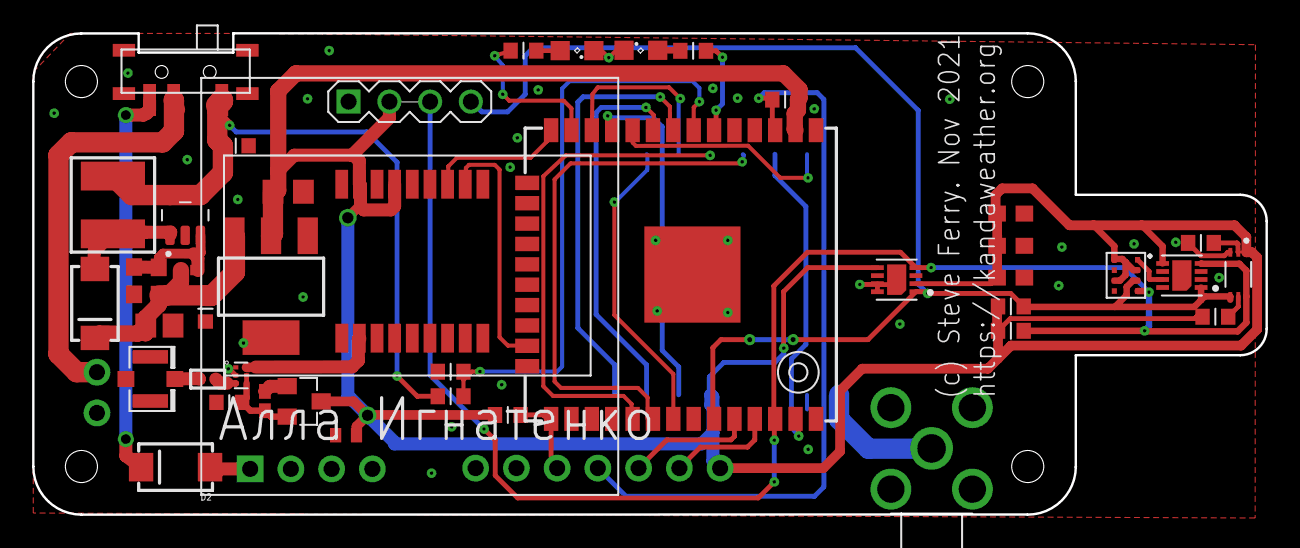
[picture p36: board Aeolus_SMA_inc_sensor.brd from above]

Board: 2 copper layers, 76.9 x 30.0 mm, 47 parts (1 on the bottom side), 38 nets.

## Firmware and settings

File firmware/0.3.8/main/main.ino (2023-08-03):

/*

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
Unless otherwise stated, all other files under this Arduino program
fall under the GPL license.

This code requires the MCCI LoRaWAN LMIC library
by IBM, Matthis Kooijman, Terry Moore, ChaeHee Won, Frank Rose
https://github.com/mcci-catena/arduino-lmic

*/

#pragma once

#include "config_hardware.h"

#include <Arduino.h>
#include <lmic.h>
//void lorawan_register(void (*callback)(uint8_t message));

#include "soc/soc.h"
#include "soc/rtc_cntl_reg.h"

#include "config_user.h"
#include "rom/rtc.h"
#include <TinyGPS++.h>
#include <Wire.h>
#include <Math.h>
#include <axp20x.h>

#include <LoraMessage.h>
#include <LoraEncoder.h>

#include <WiFi.h>

const char * APP_VERSION = "0.3.8";
String APP_VERSION_STR = "0.3.8";

// Set web server port number to 80
WiFiServer SERVER(80);
WiFiClient CLIENT;
int WIFI_DEFAULT_WINDOW = 2*60*1000;
bool WIFI_OPEN;

// Used in power management
//  Will be used to turn off GPS, check if charging, battery etc
AXP20X_Class axp;

bool SSD1306_FOUND = false;
bool BME280_FOUND = false;
bool SHT21_FOUND = false;
bool SPL06_FOUND = false;
bool AXP192_FOUND = false;
bool RELAIS_ON = false;

// Message _counter, stored in RTC memory, survives deep sleep
RTC_DATA_ATTR uint32_t COUNT = 0;

// Calculated at each step based on pressure
int MSG_INTERVAL;
bool GATEWAY_IN_RANGE;
String DOWNLINK_RESPONSE = "";
bool AUTHENTICATED = false;
bool BATT_CHARGING = false;
int8_t APPROX_UTC_HR_OFFSET = 0;
bool MESSAGE_PENDING = false;

// Launch-specific values
float SFC_PRESSURE = 0.0;
bool IF_WEB_OPENED = false;
bool IF_LAUNCHED = false;
uint8_t LAUNCH_ID[8] = { 0xFF, 0xFF, 0xFF, 0xFF, 0xFF, 0xFF, 0xFF, 0xFF } ; // For launch_id downlink
int LAUNCH_CHECK_INTERVAL = 5000;

// BME 280 environment
unsigned int TIMESTAMP;
float LATITUDE;
float LONGITUDE;
float ELEVATION_GPS;
float TEMPERATURE; // celcius
float HUMIDITY; // percent (range 0 to 100)
float PRESSURE; // hpa
float V_TEMPERATURE; // kelvin
float ELEVATION; // meters
float LUX_AVG;


// -----------------------------------------------------------------------------
// Application
// -----------------------------------------------------------------------------



//////////////////////////////////////////
///////////// ARDUINO SETUP //////////////
//////////////////////////////////////////
void setup() {
  
  // Debug
  #ifdef DEBUG_PORT
  DEBUG_PORT.begin(SERIAL_BAUD);
  #endif

  while ( millis() < 500 ); // Brief wait for serial baud

  Serial.begin(115200);

  // Buttons & LED
  pinMode(BUTTON_PIN, INPUT_PULLUP);
  pinMode(LED_PIN, OUTPUT);

  Wire.begin(I2C_SDA, I2C_SCL);
  scanI2Cdevice();

  // Display
  screen_setup();
  screen_clear();
  
  #ifndef IGNORE_TPRH_CHECK // If want to check for P,T, RH sensor
  if (!if_T_and_RH_sensor() || !if_P_sensor())
  {
    screen_print("[ERR]\n");
    screen_print("No weather sensor \n");
    screen_print("connected! Check wiring.");
    Serial.println("[ERR] No weather sensor connected!");
    delay(MESSAGE_TO_SLEEP_DELAY);
    screen_off();
    sleep_forever();
  }
  
  #endif // 
  
  // Init BME280
  bme_setup();

  // Init BH1750 and Lux variable
  light_setup();

  // Init GPS
  Serial.println("Setting up GPS (uses serial)");
  Serial.println("Note that Serial monitor may not display properly after this point.");
  delay(50); // Allow serial to catch up
  gps_setup();
  //GPS_SetHAB();

  // TTN setup
  if (!lorawan_setup()) {
    screen_print("[ERR] Radio module not found!\n");
    Serial.println("[ERR] Radio module not found!");
    delay(MESSAGE_TO_SLEEP_DELAY);
    screen_off();
    sleep_forever();
  }

   // Print initial header at top
  char screen_buff[40];
  strncpy( screen_buff, APP_VERSION, 5 );
  strncat( screen_buff, "   ", 3 );
  strncat(screen_buff, get_devname(), 12);
  strncat( screen_buff, "   ", 3);
  strncat( screen_buff, get_freq(), 3);
  screen_print(screen_buff, 0, 0);

  lorawan_register(callback);
  lorawan_sf(LORAWAN_SF);
  lorawan_adr(LORAWAN_ADR);

  Serial.println("Beginning Join attempt.");
  lorawan_join();
  if(!LORAWAN_ADR){
    LMIC_setLinkCheckMode(0); // Link check problematic if not using ADR. Must be set after join
  }

  // Show logo on first boot (if OLED attached)
  //screen_print(APP_NAME " " APP_VERSION " " DEVNAME " " get_freq(), 0, 0 ); // print firmware version in upper left corner

  Serial.println("Waiting in Join window.");
  screen_show_logo();
  screen_update();
  time_loop_wait( LOGO_DELAY ); // If Join_accept message received during this time, it will trigger LMIC callback function

  // Wait a bit longer in case OTAA response miss or poor connection
  if ( !GATEWAY_IN_RANGE )
  {
    // Listen for LoRaWAN response
    Serial.println("Waiting for OTAA Joined response.");
    screen_print("Please wait!\n\n");
    screen_print("Listening for LoRaWAN\n");
    screen_print("network coverage...\n");

    int time_check_start = millis();
    time_loop_wait( 8*1000 ); 
    while( !GATEWAY_IN_RANGE && !time_loop_check( time_check_start, 30*1000 ) )
    {
      send_status(true); // Receive possible missed join message or downlinks
      screen_update();
      time_loop_wait( 8*1000 );// Wait 5 seconds
    }
  }


  // Check that at least one confirmed message was received
  #if !defined(IGNORE_GATEWAY_CHECK)
  if (!GATEWAY_IN_RANGE) 
  { 
    screen_print("[ERR]\n");
    screen_print("No LoRaWAN coverage!\n\n");
    screen_print("Please find a better\n");
    screen_print("place outdoors.\n");
    Serial.println("[ERR] LoRaWAN network not connected!");
    delay(MESSAGE_TO_SLEEP_DELAY);
    screen_off();
    sleep_forever();
  }
  #endif

  //screen_show_qrcode();
  //screen_update();
  screen_print("LoRaWAN Connected!\n");
  screen_print("WiFi AP:  AscensionWx\n");
  screen_print("  password:  balloons\n");
  screen_print("\n");
  screen_print("Then go to  192.168.4.1\n");

  // Init wifi access point
  WiFi.softAP(SSID, PASSWORD);
  WIFI_OPEN = true;

  // Defines how async server handles GET requests
  //initServer();
  SERVER.begin();

  MSG_INTERVAL = 30000; // Status message this many millis
  uint32_t last_msg = 0;

  // Check if surface pressure has changed over 3 seconds
  uint32_t last_sfc = 0;

  while ( true ) {

    // Frequently check pressure change to see if launched
    if ( millis() - last_sfc > LAUNCH_CHECK_INTERVAL) {
      IF_LAUNCHED = checkIfLaunched();
      update_lux_avg( get_light() );
      last_sfc = millis();
    }

    if ( IF_LAUNCHED )
      break;
  
    if ( millis() - last_msg > MSG_INTERVAL) {

      // Send status message every MSG_INTERVALnumber of seconds
      //   Note that no downlinks will be able to be received, because
      //     we prioritize having checkServer() be reactive instead of
      //     just doing os_runloop_once to listen for downlinks
      send_status();
      last_msg = millis(); // store for next iteration

      wait_for_message_txcomplete();
      
    } // End status message interval loop

    if ( WIFI_OPEN ) {
      checkServer(); // Should be called frequently to check if smartphone connected
      gps_read(); // Populates time header and gets us fix progress
      screen_loop();
      os_runloop_once();
      
      if ( !IF_WEB_OPENED && millis() > WIFI_DEFAULT_WINDOW ) {
        SERVER.end();
        WiFi.softAPdisconnect(true);
        WIFI_OPEN=false;

        screen_print("\n");
        screen_print("WiFi Window Closed\n");
        screen_print("Screen will turn off soon\n");
        screen_print("\n");
        screen_print("\n");
        
      }
    }
    else // if WiFi window closed
    { 
      // Allow sleep between BME280 check
      int slp_time = LAUNCH_CHECK_INTERVAL - ( millis() - last_sfc );
      if ( slp_time > 100 ) {
        sleep_light_millis( slp_time - 50 );
        screen_off();
      }

      os_runloop_once();
      sysTimeoutCheck(); // make sure device hasn't been kept on for over 1 hour
    }

  }// End IF_LAUNCHED check

  // Reset send interval for observations
  set_msg_interval();
  
  // Turn off wifi
  if ( WIFI_OPEN )
  {
    SERVER.end(); // close access to the server
    WiFi.softAPdisconnect(true); // Ends wifi connection completely
    WIFI_OPEN = false;
  }

  Serial.println("Finished closing wifi");
  
}// End Arduino setup() method

/////////////////////////////////////////
///////////// ARDUINO LOOP //////////////
/////////////////////////////////////////
void loop() {

  int time_start = millis();
  
  // Wait a few sec for GPS to communicate NMEA sentences over Serial
  gps_time_loop_wait( GPS_WAIT );

  set_obs_timestamp();
  save_gps_data();
  read_all_sensors();

  // Note that this call sends the data sampled from the prior sleep
  print_observation();
  //Serial.println("TRANSMITTING");
  send_observation();

  //wait_for_message_txcomplete();
  time_loop_wait( LMIC_WAIT );

  int loop_time = millis() - time_start;
  int sleep_ms = MSG_INTERVAL - loop_time;
  if ( sleep_ms > 50 ) {
    //debug_print( "sleep millis", sleep_ms );
    sleep_light_millis( sleep_ms );
  }

  // Reset send interval if needed
  set_msg_interval();

  // Check that unphysical time limit isn't reached
  sysTimeoutCheck(); 

}

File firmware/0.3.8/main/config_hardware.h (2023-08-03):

#define DEBUG_PORT              Serial      // Serial debug port
#define SERIAL_BAUD             115200      // Serial debug baud rate

#ifdef DEBUG_PORT
#define DEBUG_MSG(...) DEBUG_PORT.printf( __VA_ARGS__ )
#else
#define DEBUG_MSG(...)
#endif

// -----------------------------------------------------------------------------
// General
// -----------------------------------------------------------------------------

#define I2C_SDA         21
#define I2C_SCL         22
#define LED_PIN         14
#define RELAIS_PIN         14   // Works with TTGO LoRa32 V2.1 board (confirmed)
#define BUTTON_PIN      39

// -----------------------------------------------------------------------------
// OLED
// -----------------------------------------------------------------------------

#define SSD1306_ADDRESS 0x3C

// -----------------------------------------------------------------------------
// T, Pressure, Humidity
// -----------------------------------------------------------------------------

#define BME280_ADDRESS_0x76 0x76
#define BME280_ADDRESS_0x77 0x77
#define SPL06_ADDRESS_0x76 0x76
#define SPL06_ADDRESS_0x77 0x77
#define SHT21_ADDRESS 0x40

// -----------------------------------------------------------------------------
// GPS
// -----------------------------------------------------------------------------

#define GPS_BAUDRATE    9600
#define USE_GPS         1
#define ss              Serial2 // define GPSserial as ESP32 Serial2
#define LMIC_WAIT       3000 // The lmic library requires minimum of 2.7 seconds to complete RX2 (maybe more if SF10 to SF12)
#define GPS_WAIT        1900 // Should be longer than 1 second (default on GPS)

// Options on ESP32 are:
//   RX: 3   TX: 1    == Serial0
//   RX: 9   TX: 10   == Serial1
//   RX: 16  TX: 17   == Serial2

#define GPS_RX_PIN      1
#define GPS_TX_PIN      3
#define GPS_POWER_PIN   AXP192_LDO3

// -----------------------------------------------------------------------------
// LoRa SPI
// -----------------------------------------------------------------------------

#define SCK_GPIO        5
#define MISO_GPIO       19
#define MOSI_GPIO       27
#define NSS_GPIO        18
#define RESET_GPIO      23
#define DIO0_GPIO       26
#define DIO1_GPIO       33
#define DIO2_GPIO       32

#define CLOCK_ERROR             1

// -----------------------------------------------------------------------------
// AXP192 (Rev1-specific options)
// -----------------------------------------------------------------------------

#define AXP192_SLAVE_ADDRESS  0x34
#define GPS_POWER_CTRL_CH     3
#define LORA_POWER_CTRL_CH    2
#define PMU_IRQ               35

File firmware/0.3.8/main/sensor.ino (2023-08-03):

/***************************************************************************
  This is a library for the BME280 humidity, temperature & pressure sensor
  Designed specifically to work with the Adafruit BME280 Breakout
  ----> http://www.adafruit.com/products/2650
  These sensors use I2C or SPI to communicate, 2 or 4 pins are required
  to interface. The device's I2C address is either 0x76 or 0x77.
  Adafruit invests time and resources providing this open source code,
  please support Adafruit andopen-source hardware by purchasing products
  from Adafruit!
  First written by Limor Fried & Kevin Townsend for Adafruit Industries.
  BSD license, all text above must be included in any redistribution
  See the LICENSE file for details.

  Regarding calculation of elevation:
    - It's only possible with a rising sensor
    - The approximation is made under the assumption of 
         hydrostatic balance (almost always) in meteorology
    - Written by Nicolas Lopez - Kanda Weather Group LLC
    - kandaweather@gmail.com
  
 ***************************************************************************/

#include <Wire.h>
#include <Adafruit_Sensor.h>
#include <Adafruit_BME280.h>
#include <SHT21.h>
#include <SPL06-007.h>
#include <BH1750.h>

char bme_char[32]; // used to sprintf for Serial output

Adafruit_BME280 bme; // I2C
SHT21 sht;
BH1750 lightMeter;
  
float v_temperature_last;
float elevation_last;
float pressure_last;

const uint8_t psfc_len = 4;
float psfc_data[ psfc_len ];

// Keeps last 60 seconds
const int lux_increment = 5; // 5 seconds per datapoint
const int lux_window = 60*5; // save last 5 minutes
const uint8_t lux_len = lux_window/lux_increment;
float lux_data[ lux_len ];
uint32_t last_lux_update = 0;

void bme_setup() {

    bool status;
    
    if (BME280_FOUND) {
       status = bme.begin( BME280_ADDRESS_0x76 );
       if (!status) // if still not found, try 0x77
          status = bme.begin( BME280_ADDRESS_0x77 );
    }
    else if (SPL06_FOUND) {
      SPL_init( ); // Has hardcoded 0x77 into the library function
      status = true;
    }
    
    if (!status ) {
        Serial.println("Could not find a valid weather sensor, check wiring!");
    }

    // Wake up sensor
    delay(20);
    get_pressure_hpa();
    delay(500);
    
    // Take first guess at surface pressure
    while (SFC_PRESSURE < 150.0 || SFC_PRESSURE > 1020.0)
    {
      // Note THAT SPL06_001 sensor currently does not work properly.
      SFC_PRESSURE = get_pressure_hpa();
      delay(500);
    }

    int i = 0;
    while( i < 4 )
    {
      psfc_data[i] = 0;
      i++;
    }

    // Compute prior variables
    pressure_last = SFC_PRESSURE;
    v_temperature_last = calc_v_temperature( get_raw_temperature(), 
                                             get_humidity(), 
                                             pressure_last );
    elevation_last = 0;

}

void light_setup()
{
  lightMeter.begin();

  // Set all lux values to 0
  for (int i = 0; i < lux_len; i++) {
    lux_data[i] = 0.0;
  }
  
}

void read_all_sensors() {
  
      // Store the last variables
      pressure_last = PRESSURE;
      v_temperature_last = V_TEMPERATURE;
      elevation_last = ELEVATION;
  
      // Update environment state
      time_loop_wait(20); // BME280 has sample rate of 100Hz
      TEMPERATURE = get_raw_temperature();
      time_loop_wait(20); 
      HUMIDITY = get_humidity();
      time_loop_wait(20);
      PRESSURE = get_pressure_hpa(); // Store as hpa

      // get the lux value and calibrate the temperature
      LUX_AVG = update_lux_avg( get_light() );
      calibrateTemperature();

      // Calculate virtual temperature given new values
      V_TEMPERATURE = calc_v_temperature( TEMPERATURE, 
                                              HUMIDITY, 
                                              PRESSURE );

      // Finally we use new virtual temperature in 
      ELEVATION = calc_elevation();
}

float update_lux_avg( float lux )
{

  if ( last_lux_update == 0 ) {
    last_lux_update = millis();
    return 0.0;
  }

  // Convert ms to seconds
  float interval = (millis() - last_lux_update)/1000;
  int increment = round(interval / lux_increment);
  
  // Shift all the data back by interval
  for (int i = lux_len-1; i > increment-1; i--){        
    lux_data[i]=lux_data[i-increment];
  }

  // Populate initial parts of the array
  for (int i=0; i < increment; i++)
    lux_data[i] = lux;

  // Finally get the average of the list
  float total = 0;
  for (int i = 0; i < lux_len; i++) {
    total = total + lux_data[i];
  }

  last_lux_update = millis();

  float avg = total/lux_len;
  return avg;
}

void calibrateTemperature() {
  
  float internal_offset = 0;
  if ( BME280_FOUND ) internal_offset = 1.2; // bme280 is known to self-heat

  // Daytime/sunny enclosure heating plus ambient light in aperture
  // This offset is enclosure-specific, and 
  //    should be physically tested in several daylight/cloudy conditions.
  // At night might give small non-zero results if there is blinking light somewhere inside the enclosure
  float sunlight_offset = LUX_AVG/7000.0; 

  //debug_print("sunlght offset", sunlight_offset);

  TEMPERATURE = TEMPERATURE - (internal_offset + sunlight_offset);
}

float get_humidity() {
    float rh = MISSING_FLOAT;
    if ( BME280_FOUND ) rh = bme.readHumidity();
    else if ( SHT21_FOUND ) rh = sht.getHumidity();
    
    return rh;
}

float get_pressure_hpa() {
    float p = MISSING_FLOAT;
    if ( BME280_FOUND ) p = bme.readPressure() / 100.0; // convert to hpa
    // be careful... get_pressure referenced below is spl06 library function
    else if ( SPL06_FOUND ) p = get_pressure(); // returns already in hpa

    return p;
}

float get_raw_temperature() {
    float t = MISSING_FLOAT;
    if ( BME280_FOUND ) t = bme.readTemperature();
    else if ( SHT21_FOUND ) t = sht.getTemperature();
    
    return t;
}

float get_light()
{
  float lux = lightMeter.readLightLevel();
  //debug_print("Light", lux);
  return lux;
}

float calc_v_temperature(float t, float rh, float p) {
  
  // calc saturation vapor pressure es(T)
  // https://journals.ametsoc.org/jamc/article/57/6/1265/68235/A-Simple-Accurate-Formula-for-Calculating
  float es;
  if ( t>0 )
  {
    es = exp( 34.494 - (4924.99/(t+237.1)) ) /  pow(t+105, 1.57);
  } else {
    es = exp( 43.494 - (6545.8/(t+278)) ) /  pow(t+868, 2);
  }
  
  // calc actual vapor pressure using  rh = e/es
  float e = (rh/100)*es;
  e = e/100.0; // Convert to hpa
  
  // calc mixing ratio
  float w = 0.62197 * (e / (p-e));

  // calc virtual temperature in Kelvin
  float tv = (1+(0.61*w))*(t+273.15);

  return tv;
  
}
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

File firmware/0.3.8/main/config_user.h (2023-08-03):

// -----------------------------------------------------------------------------
// User Configuration
// -----------------------------------------------------------------------------

//#define DEBUG_MODE 1  // Begins flight observations 2 minutes after WiFi  //NICK
//#define IGNORE_GATEWAY_CHECK 1 // NOTE: Helium and other OTAA should ignore gateway check regardless
//#define IGNORE_TPRH_CHECK 1 // Uncomment to allow no I2C solder for T,P, RH

// Choose an option
//#define HELIUM 1
//#define TTN 1

#define USE_OTAA 1

#define MSG_INTERVAL_150M          10000 // Observation interval for first 150 meters

#define MSG_INTERVAL_950           5000 // hpa
#define MSG_INTERVAL_900           5000      
#define MSG_INTERVAL_800           10000     
#define MSG_INTERVAL_700           10000     
#define MSG_INTERVAL_600           20000
#define MSG_INTERVAL_500           20000
#define MSG_INTERVAL_400           20000
#define MSG_INTERVAL_300           20000
#define MSG_INTERVAL_200           20000

// If using a single-channel gateway, uncomment this next option and set to your gateway's channel
//#define SINGLE_CHANNEL_GATEWAY  0

#define FORCE_IF_LAUNCHED_HPA   960   // Forcefully set if_launched to true if this level is reached

#define MESSAGE_TO_SLEEP_DELAY  5000        // Time after message before going to sleep
#define LOGO_DELAY              5000        // Time to show logo on first boot
#define QRCODE_DELAY            10000        // Time to show logo on first boot
#define OBSERVATION_PORT        81          // Port the obs messages will be sent to
#define STATUS_PORT             82          // Port the status messages will be sent to
#define AUTHENTICATION_PORT     83          // Port for authentication message
#define LORAWAN_CONFIRMED_EVERY 0           // Send confirmed message every these many messages (0 means never)
#define LORAWAN_SF              DR_SF10     // Spreading factor
#define LORAWAN_ADR             0           // Enable ADR

#define MISSING_UINT            0
#define MISSING_FLOAT           0

//Wifi defines
const char* SSID     = "AscensionWx";
const char* PASSWORD = "balloons";

// Define here for later implementation
void debug_print(String name, float val );

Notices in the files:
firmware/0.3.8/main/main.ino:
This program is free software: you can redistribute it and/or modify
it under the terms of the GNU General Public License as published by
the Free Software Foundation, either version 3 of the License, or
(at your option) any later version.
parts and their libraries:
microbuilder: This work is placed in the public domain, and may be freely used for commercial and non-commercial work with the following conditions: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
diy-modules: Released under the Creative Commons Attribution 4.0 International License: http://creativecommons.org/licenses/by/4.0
